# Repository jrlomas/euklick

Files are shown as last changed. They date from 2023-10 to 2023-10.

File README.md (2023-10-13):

# Euklick BETA

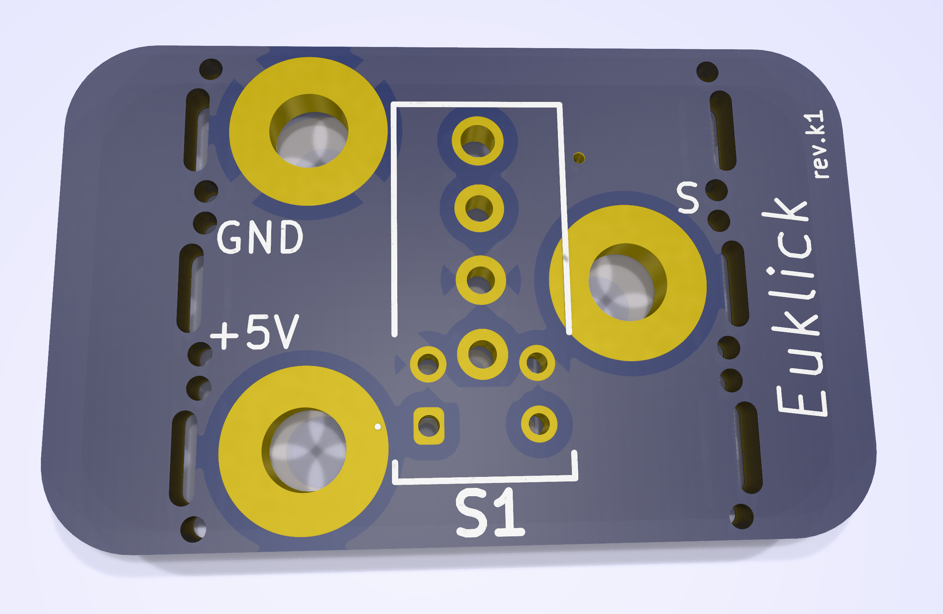
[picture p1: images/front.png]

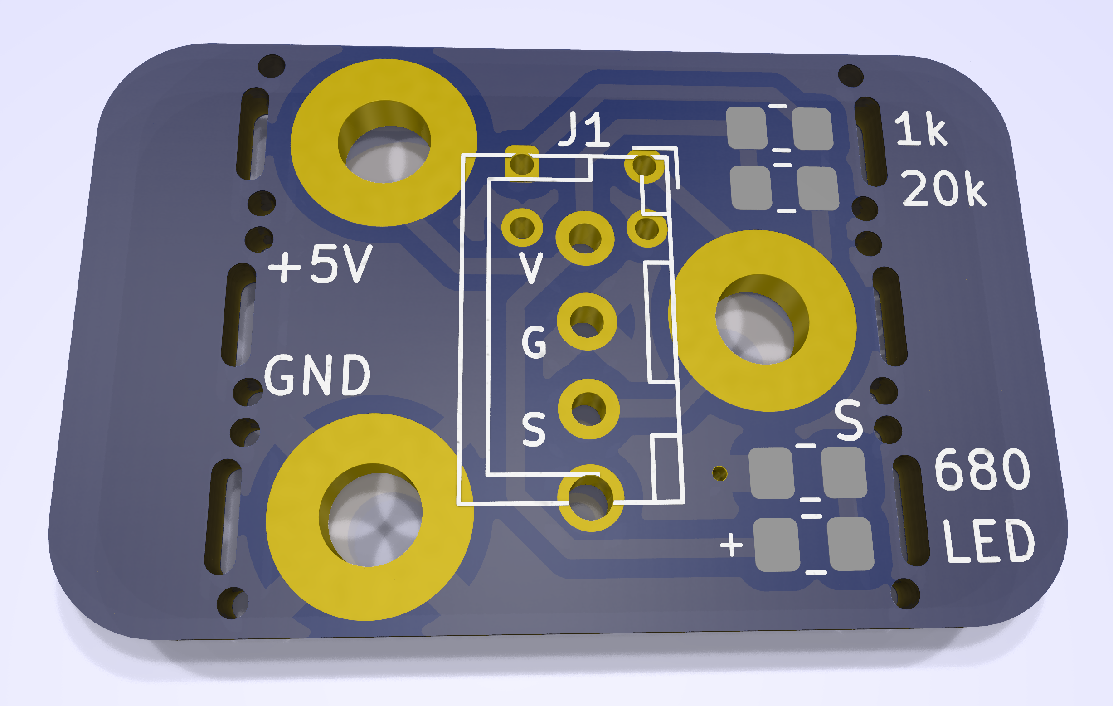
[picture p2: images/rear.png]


Single PCB 5V optical probe for 3D printers.  Euklick is meant to work with the new Omron optical microswitches of the [D2FP series](https://www.mouser.com/datasheet/2/307/Omron_08182023_D2FP_Datasheet_English-3305532.pdf), specifically the [D2FP-FN2](https://www.mouser.com/ProductDetail/653-D2FP-FN2).  This switch is rated to a *minimum* of **70,000,000** operations, and much tighter tolerances at the time the switch is pressed.

# The PCB, standing on the shoulder of giants
The PCB borrows, known euphemistically in the music industry as *sampling*, from the designs of the Euclid probe and PCBKlicky.  Unlike PCBKlicky, however, to lower the cost and streamline ordering boards from manufacturers, it makes use of a single board that can be used for both the microswitch (probe), and toolhead side.  Although not necessary, when the board is used in its toolhead holder, the wings / leaves at the end of the board can be snapped as to provide a tighter fit to the plastic parts.  There are cutouts and mouse bites that make it possible to snap the ends, with some force.  The board is mostly compatible with PCBKlicky; nonetheless, the switch is slightly offset from the centerline of the PCB since the pinout for the optical switch changed from the inline package of the older D2F physical switches.  This change makes it possible for the mounted magnets to avoid the soldering pads of the optical switch, while re-using the original magnet positions.
Unlike PCBKlicky, the board only supports 5V as its source of power, and power is not optional (since the optical switch requires active power).

# BOM

| Item | Quantity | Notes |
| --- | --- | --- |
| toolhead PCB | 2 | [gerber files](euklick_production/euklick.zip), [bom](euklick_production/bom.csv), and [cpl](euklick_production/positions.csv) files to order |
| 1K 0850 Resistor | 1 ||
| 20k 0850 Resistor | 1|  Pull-up resistor any value between 10k and 50k|
| 680R 0805 Resistor | 1 | LED resistor |
| 0805 LED | 1 | Any color of your choice |
| JST-XH 3 pin header | 1 | |
| JST-XH 3 wire pigtail connector | 1| |
| pair of countersunk, matching magnets | 5 | [source](https://www.kjmagnetics.com/proddetail.asp?prod=R422CS-P&cat=15)|
| M2x3.2x4mm heatset inserts | 10 | |
| Omron D2FP-FN2 optical switch | 1 | [source](https://www.mouser.com/ProductDetail/653-D2FP-FN2)|
| Self-tapping stainless torx drive M2 screws | 3 | |
| M3x6mm flat head screws | 2 | |

# Assembly
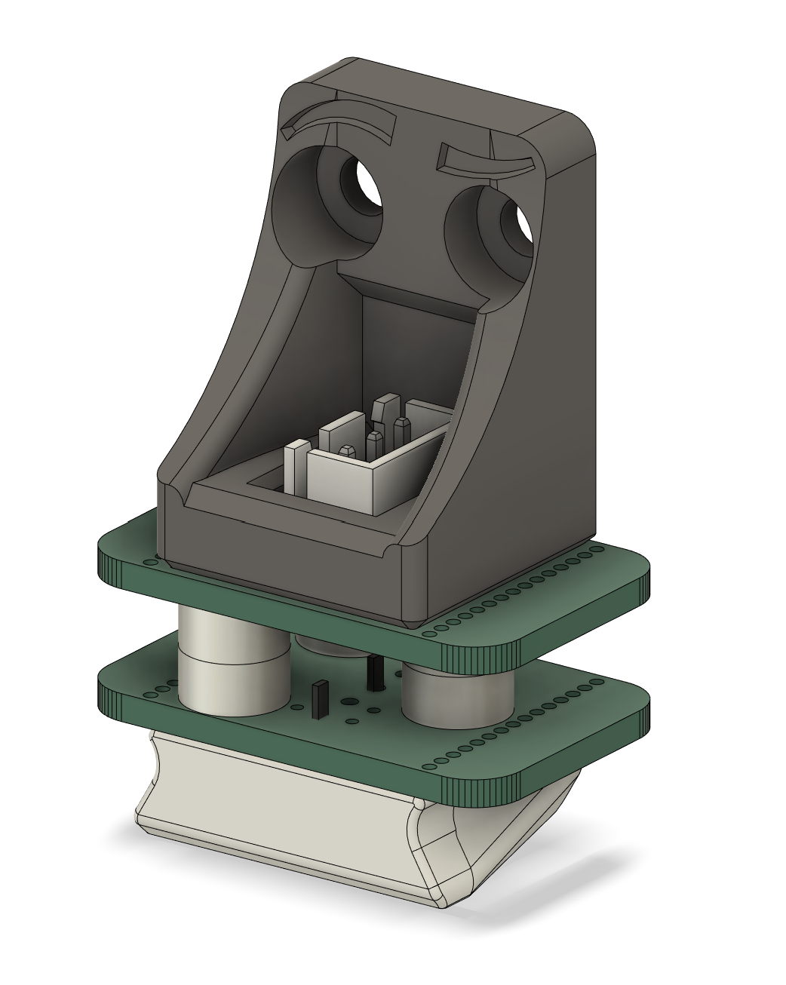
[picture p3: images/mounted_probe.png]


Two of the boards have to be used for assembly.
For the upper board (board attach to the toolhead), only the JST 3 pin header is necessary, along with three countersunk magnets.  Optionally, the *wings* on the board can be snapped along the provided mouse bites line.

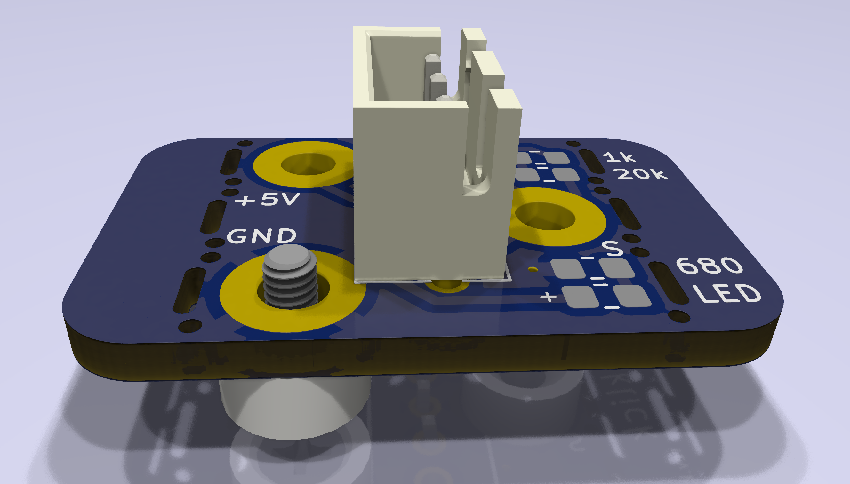
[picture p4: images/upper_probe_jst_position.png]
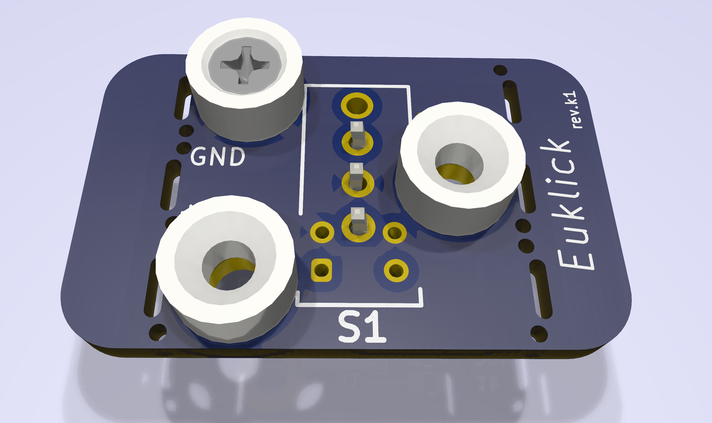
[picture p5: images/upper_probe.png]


For the lower board the switch should be attached from the side marked S1 as here, and the rear of the board should be populated

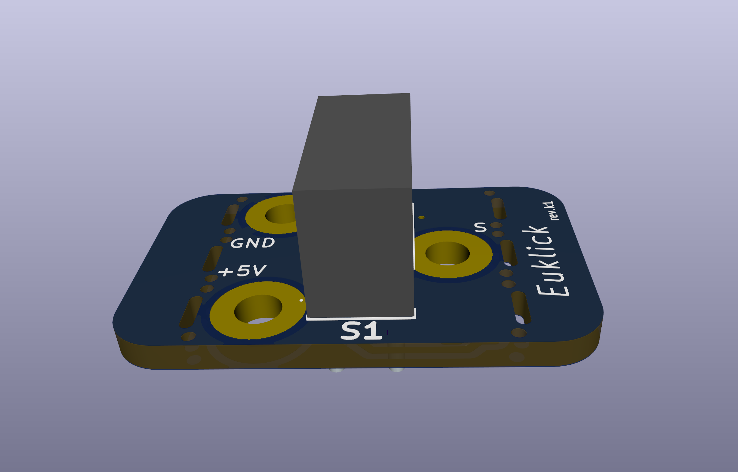
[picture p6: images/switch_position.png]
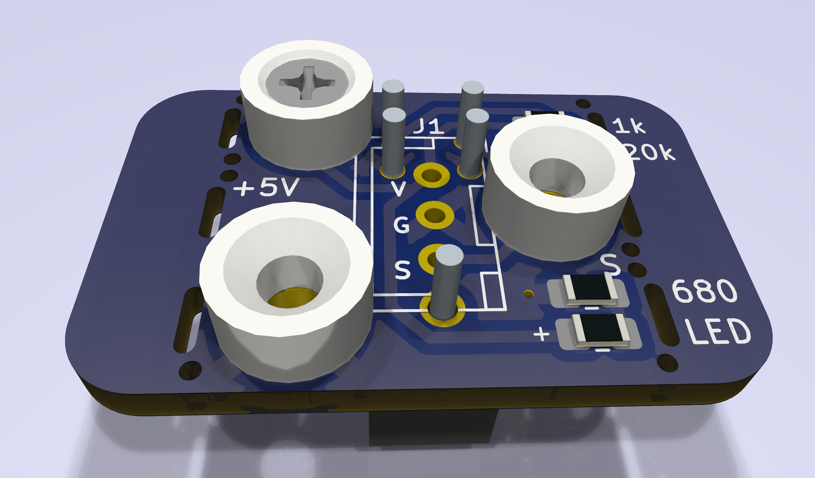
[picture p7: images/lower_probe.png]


# License
Free for personal non-comercial use, see the [license](LICENSE.md).  I am [knight_rad.iant](https://discord.com/users/1038855498696499321) on Discord.

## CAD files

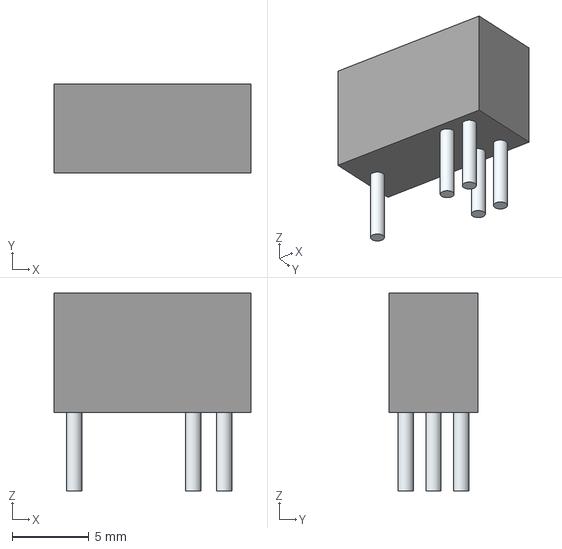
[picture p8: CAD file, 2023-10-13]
D2FP/D2FP-FN2.stp
12.8 x 5.80 x 12.8 mm
Leads

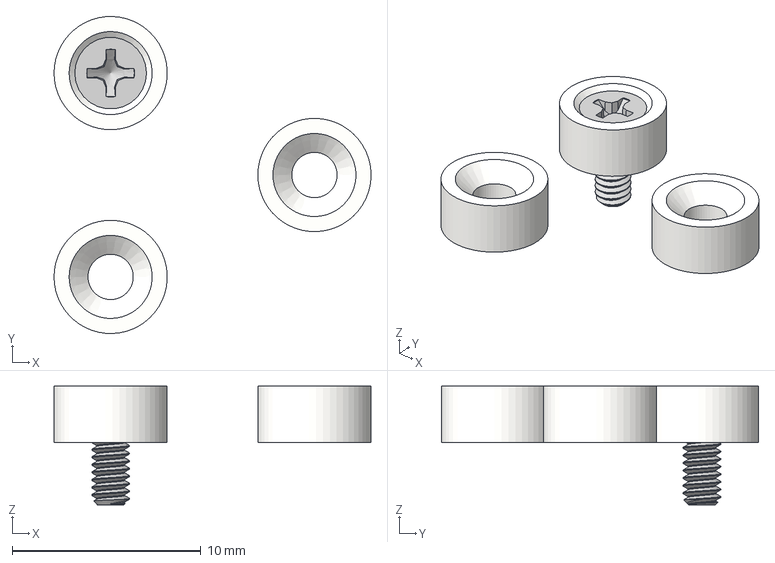
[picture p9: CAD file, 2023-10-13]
magnets.step
16.8 x 16.8 x 6.30 mm

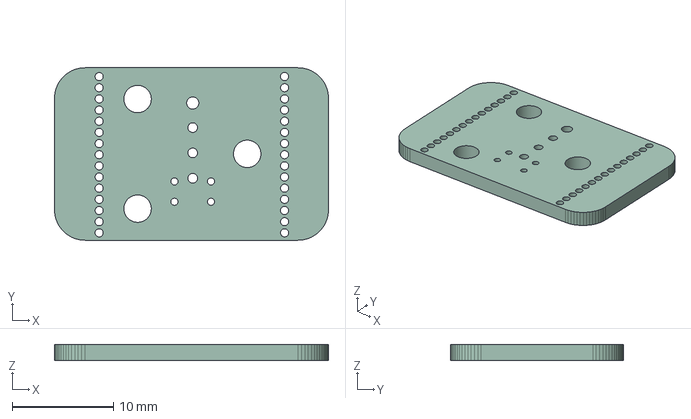
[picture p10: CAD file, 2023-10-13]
euklick.step
27.0 x 17.0 x 1.60 mm

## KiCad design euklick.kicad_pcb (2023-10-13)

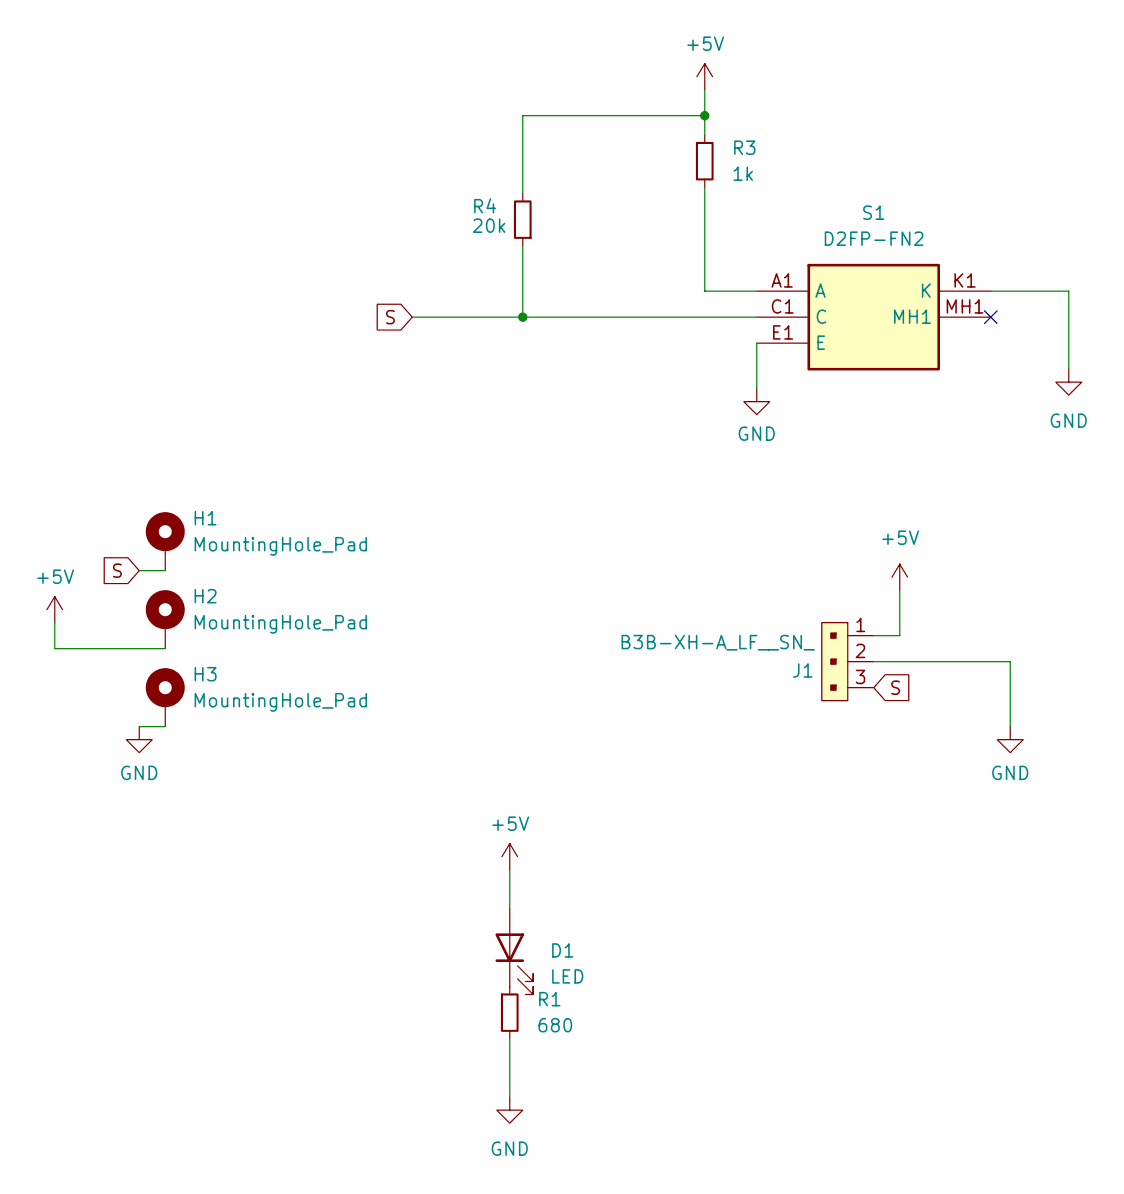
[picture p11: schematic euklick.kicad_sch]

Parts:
D1: LED; LED_0805_2012Metric_Pad1.15x1.40mm_HandSolder; LCSC Part C84256
H1, H2, H3: MountingHole_Pad; MountingHole_2.7mm_Pad
J1: B3B-XH-A_LF__SN_; JST_XH_B3B-XH-A_1x03_P2.50mm_Vertical; MPN B3B-XH-A(LF)(SN); Digi-Key_PN 455-2248-ND
R1: 680; R_0805_2012Metric_Pad1.20x1.40mm_HandSolder
R3: 1k; R_0805_2012Metric_Pad1.20x1.40mm_HandSolder
R4: 20k; R_0805_2012Metric_Pad1.20x1.40mm_HandSolder
S1: D2FP-FN2; D2FPFN2; Manufacturer_Part_Number D2FP-FN2

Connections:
+5V: D1.2 (A), H2.1, J1.1, R3.1, R4.2
GND: H3.1, J1.2, R1.2, S1.E1 (E), S1.K1 (K)
unnamed: D1.1 (K), R1.1
unnamed: R3.2, S1.A1 (A)
S: H1.1, J1.3, R4.1, S1.C1 (C)

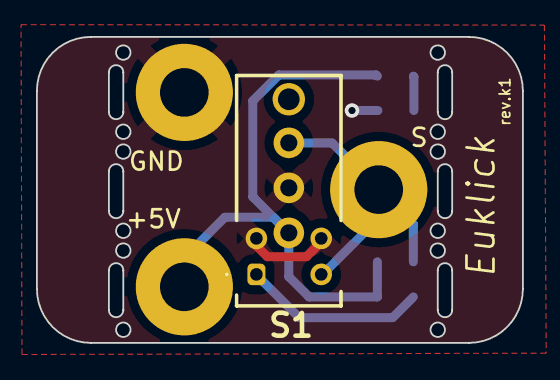
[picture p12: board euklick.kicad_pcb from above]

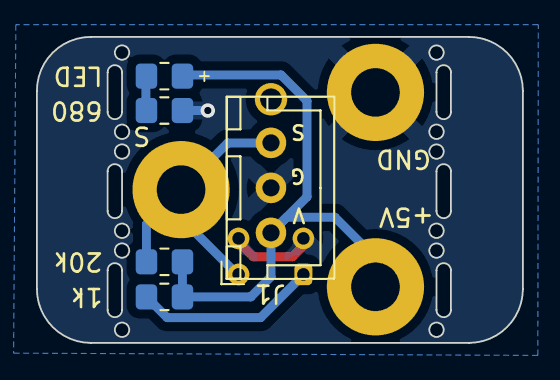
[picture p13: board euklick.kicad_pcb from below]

Board: 2 copper layers, 27.0 x 17.0 mm, 9 parts (5 on the bottom side), 5 nets.

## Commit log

2023-10-13 Initial working commit
    [euklick.kicad_pcb, euklick.kicad_sch, euklick.step]
2023-10-13 New instructions
    [D2FP-FN2.stp, euklick.kicad_pcb, euklick.kicad_sch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]
2023-10-13 added Gerbers for production and updated readme
2023-10-13 Updated BOM in README to include resistors and led
